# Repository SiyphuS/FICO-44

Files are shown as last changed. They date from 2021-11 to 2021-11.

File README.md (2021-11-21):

# 项目简介
项目名称：FICO-44  
简介视频：https://www.bilibili.com/video/BV1Yh41147wo/

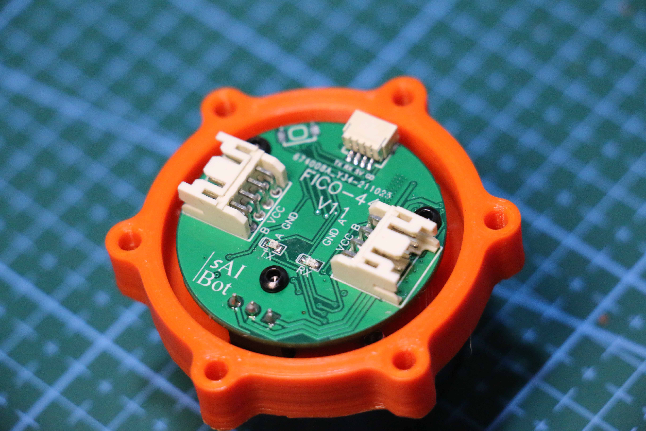
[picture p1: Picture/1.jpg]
主控板


***当前版本仍存在较大缺陷，仅供研究用***  
PCB工程 https://oshwhub.com/zhang_sai/44-guan-jie-qu-dong

## 特点：  
* 基于SIMPLE FOC实现的BLDC FOC（无电流环）控制，控制板集成控制、驱动、编码器于一体； 
* **单个关节80元左右的物料成本**
* 采用集成两级行星减速器，减速比达到30；  
* 除轴承、螺钉、螺母外，所有结构件采用3D打印，大大降低成本。  

## 参数
* 额定电压：16V  
* 额定功率：25W  
* 最大扭矩：1N·M（预估，可能误差较大）  
* 最高转速：80RPM  
* 峰值电流：2.5A  

## 缺陷
* **缺少电流环，高负载、快速运动时极易跑飞，导致当前版本可用性较差。正在考虑保持成本不会大幅上升的解决方案**  
* **3D打印行星减速器的齿轮、齿圈时，打印机精度不足导致装配有问题或者运动过程中阻力过大。使用ENDER-3S打印机，PLA耗材，调教打印机到良好状态时成品率较高，摩擦力可接受。**  

## 提示
* 3D打印的模型需要根据自己的打印机型号和状态进行动态调整后输出STL文件打印，涉及过盈配合和齿轮传动
* 电机一定要让商家做成不带限位的，否则...

## 使用说明
LGT8F328P环境搭建指南：https://oshwhub.com/costar/larduino

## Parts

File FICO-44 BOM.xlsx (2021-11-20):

序号 | 名称 | 数量 | 单价 | 参考链接 | 备注
1 | 轴承 4*7*2.5 | 6 | 1.2 | https://detail.tmall.com/item.htm?id=611796709407&_u=kpuvnbmcd85&skuId=4777422306653
2 | 轴承 优质级B6706ZZ 30*37*4mm | 1 | 5.7 | https://detail.tmall.com/item.htm?id=634910663174&spm=a1z09.2.0.0.9b972e8dt52oDc&_u=kpuvnbma774
3 | PHD2.0线 | 1 | 2 | https://item.taobao.com/item.htm?spm=a1z09.2.0.0.9b972e8dt52oDc&id=621085087437&_u=kpuvnbm18de | 双头同向 长度自选
4 | USB转485模块 | 1 | 2.65 | https://item.taobao.com/item.htm?spm=a1z09.2.0.0.9b972e8dt52oDc&id=537106634975&_u=kpuvnbmf10a
5 | 预埋螺母 3*4*5 | 6 | 0.05 | https://detail.tmall.com/item.htm?id=19528296472&spm=a1z09.2.0.0.9b972e8dt52oDc&_u=kpuvnbm7ba9
6 | 预埋螺母 2*3.5*4 | 12 | 0.05 | 同上
7 | 螺钉 M2*16沉头内六角 | 6 | 0.1 | https://detail.tmall.com/item.htm?id=521341457404&spm=a1z09.2.0.0.9b972e8dt52oDc&_u=kpuvnbm6b46
8 | 螺钉 M2*4圆头内六角 | 3 | 0.1 | https://detail.tmall.com/item.htm?id=521341125910&_u=kpuvnbma651&skuId=4321899528386
9 | 螺钉 M2*6圆头内六角 | 3 | 0.1 | 同上
10 | 螺钉 M2*5内六角 | 6 | 0.1 | https://detail.tmall.com/item.htm?id=521303174891&spm=a1z09.2.0.0.9b972e8dt52oDc&_u=kpuvnbm53db
11 | 螺钉 M3*6圆头十字 | 6 | 0.1 | https://detail.tmall.com/item.htm?id=521140346640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
12 | 2804云台电机 | 1 | 35 | https://detail.1688.com/offer/602427933286.html?spm=a360q.8274423.0.0.49c84c9awkLhvP | 给厂家备注不需要限位
13 | 润滑脂 | 1 | 8 | https://item.taobao.com/item.htm?spm=a1z09.2.0.0.779d2e8dTmLkBQ&id=622524727704&_u=kpuvnbm0513

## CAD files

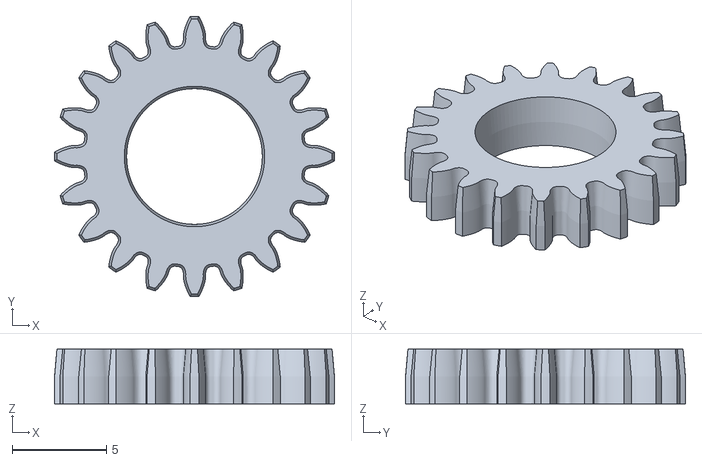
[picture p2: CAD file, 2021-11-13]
3D file/STL/44xxc-2.stl
14.9 x 14.9 x 2.89

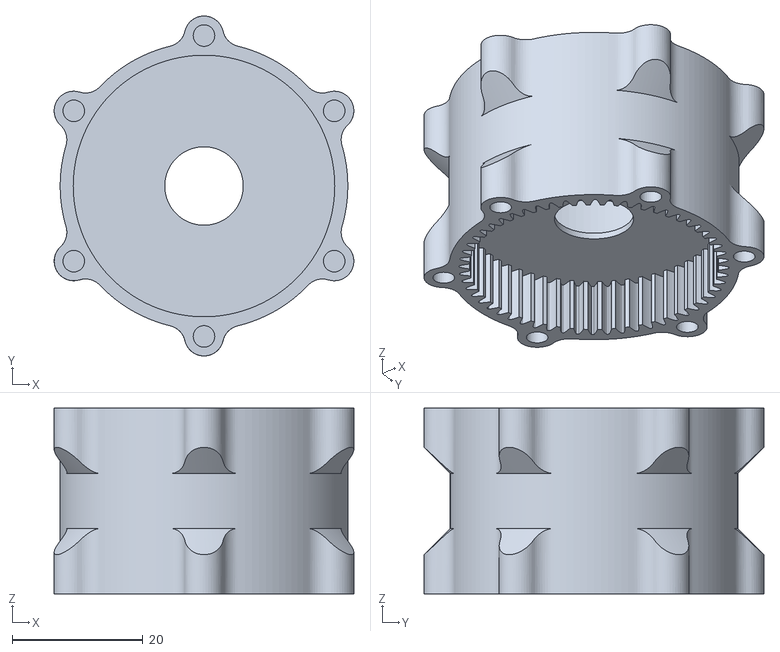
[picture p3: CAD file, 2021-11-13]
3D file/STL/44wcq.stl
45.8 x 52.0 x 28.4

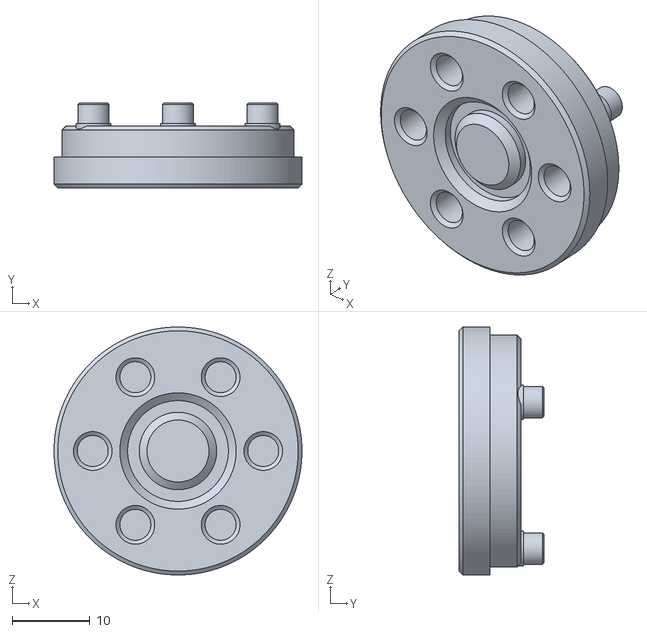
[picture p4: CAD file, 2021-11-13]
3D file/STL/44scz.stl
32.0 x 11.0 x 32.0

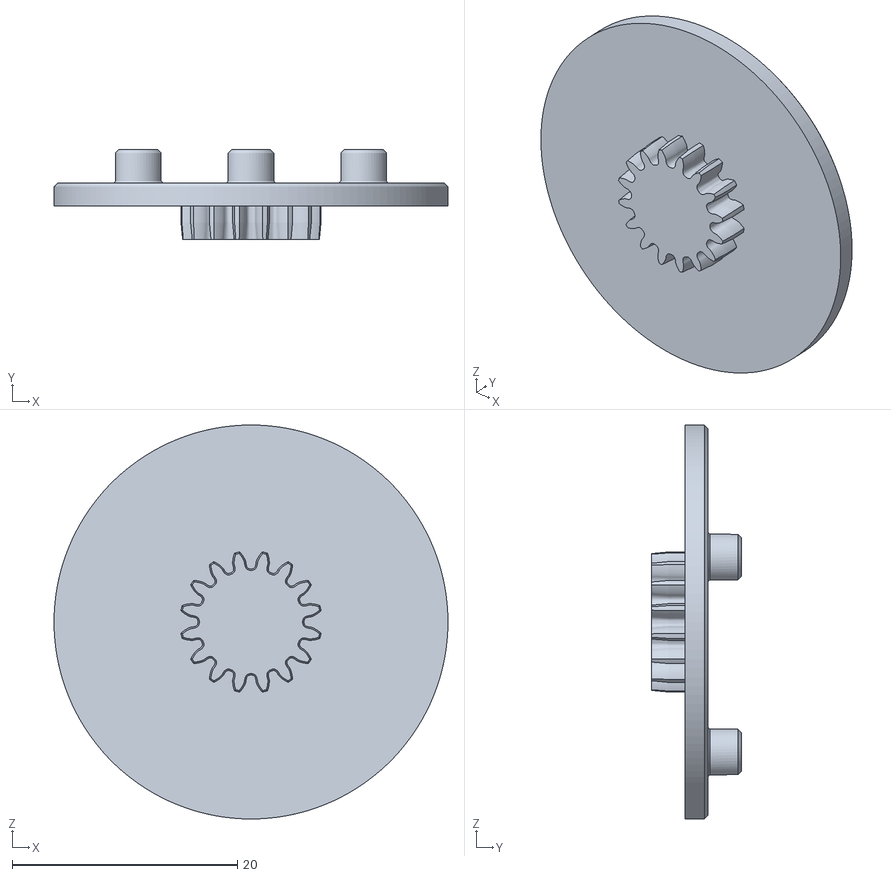
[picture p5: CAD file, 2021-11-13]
3D file/STL/44xxj.stl
35.0 x 8.00 x 35.0

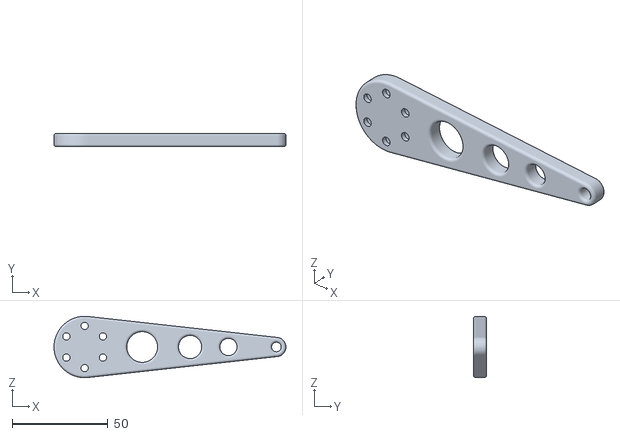
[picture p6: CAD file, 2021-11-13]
3D file/STL/44lb.stl
121.0 x 7.00 x 32.0

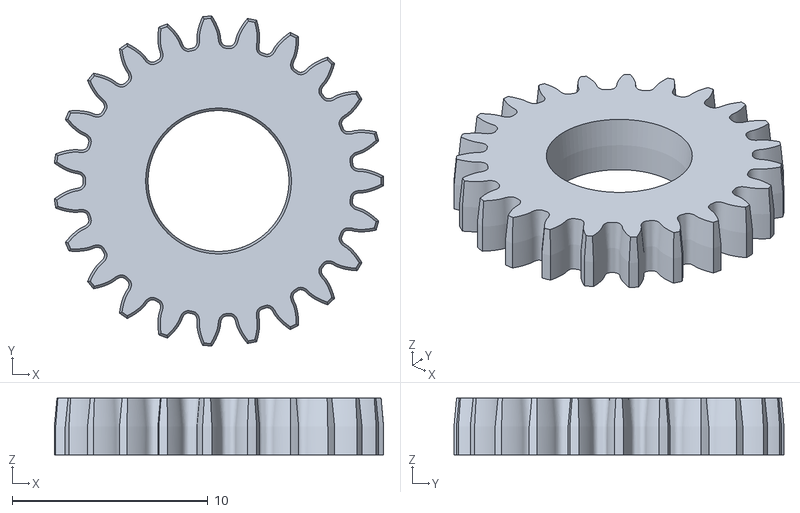
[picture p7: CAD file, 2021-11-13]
3D file/STL/44xxc-1.stl
16.8 x 16.9 x 2.89

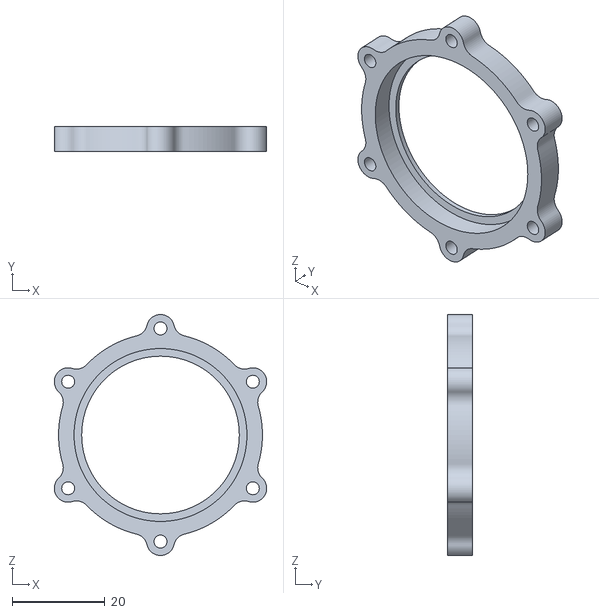
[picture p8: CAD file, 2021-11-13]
3D file/STL/44zg.stl
45.8 x 5.30 x 52.0

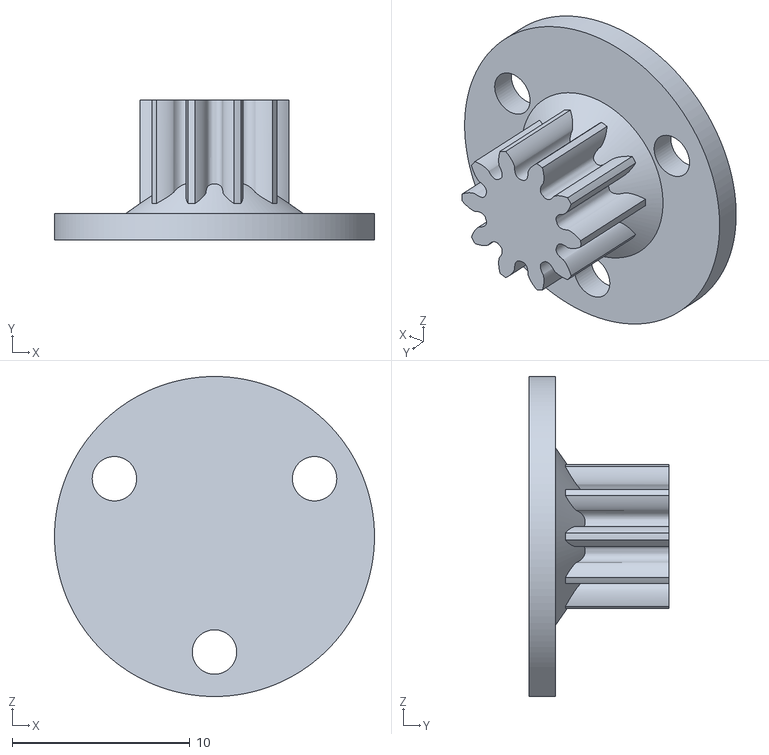
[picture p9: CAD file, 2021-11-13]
3D file/STL/44srz.stl
18.0 x 7.90 x 18.0

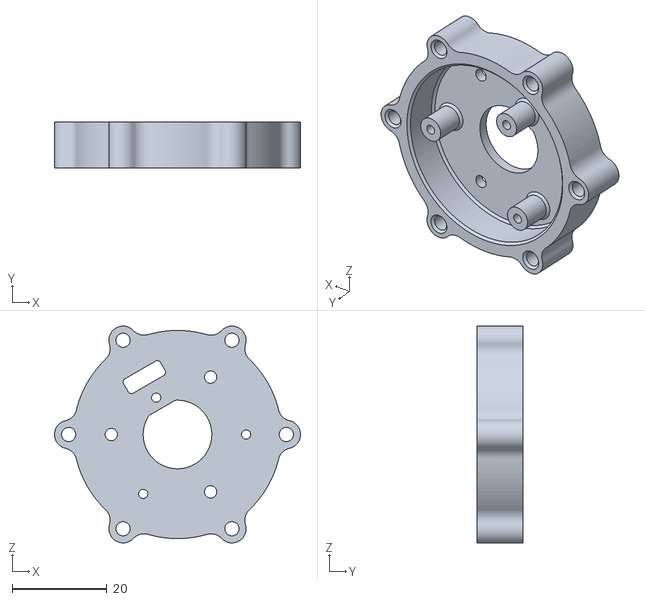
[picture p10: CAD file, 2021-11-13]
3D file/STL/44djz.stl
52.0 x 9.70 x 45.8

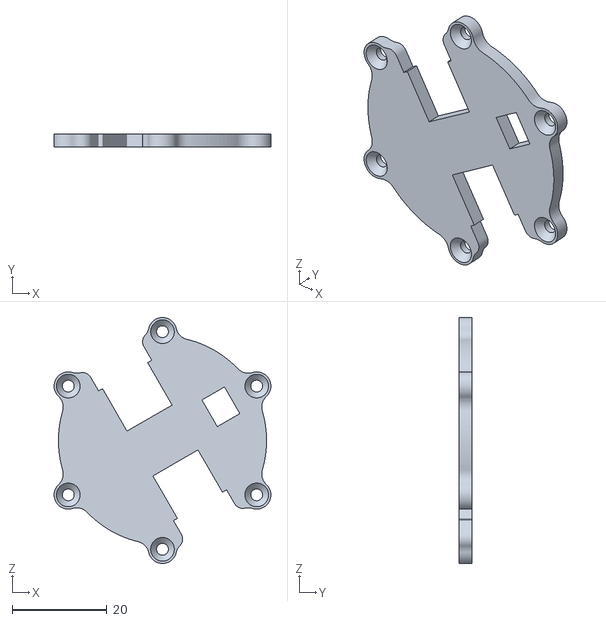
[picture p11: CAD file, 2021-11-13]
3D file/STL/44dg.stl
45.8 x 2.80 x 52.0

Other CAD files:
3D file/30-37-4轴承.prt
3D file/4-7-2_5轴承.prt
3D file/44二级太阳轮1.prt
3D file/44外齿圈.prt
3D file/8-12-3磁环.prt
3D file/PCB/___0_1_1_15__1.prt
3D file/PCB/___0_1_1_15__2.prt
3D file/PCB/___0_1_1_15__3.prt
3D file/PCB/___0_1_1_15__4.prt
3D file/PCB/___0_1_1_15__5.prt
3D file/PCB/___0_1_1_15__6.prt
3D file/PCB/___0_1_1_15__7.prt
3D file/PCB/___0_1_1_15__8.prt
3D file/PCB/___0_1_1_15__9.prt
3D file/PCB/compound-157.prt
3D file/PCB/compound-51006_1.prt
3D file/PCB/compound-51006_2.prt
3D file/PCB/compound-51006_3.prt
3D file/PCB/compound-51006_4.prt
3D file/PCB/compound-51006_5.prt
3D file/PCB/compound-51006_6.prt
3D file/PCB/compound-51006_7.prt
3D file/PCB/compound-51006_8.prt
3D file/PCB/compound-51006_9.prt
3D file/PCB/compound-6247_1.prt
3D file/PCB/compound-6247_10.prt
3D file/PCB/compound-6247_11.prt
3D file/PCB/compound-6247_12.prt
3D file/PCB/compound-6247_2.prt
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

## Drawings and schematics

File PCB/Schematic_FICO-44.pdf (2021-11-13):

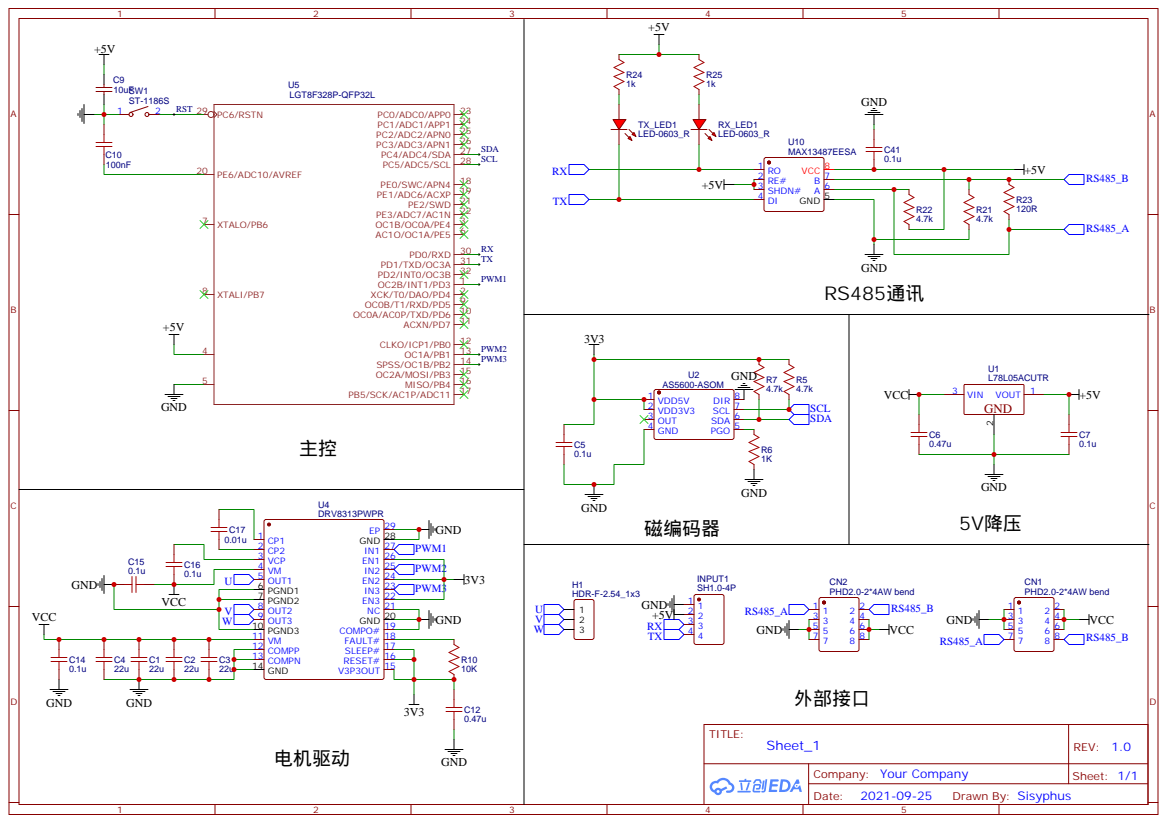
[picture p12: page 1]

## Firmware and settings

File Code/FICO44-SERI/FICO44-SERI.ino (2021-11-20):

/**
   Comprehensive BLDC motor control example using magnetic sensor

   Using serial terminal user can send motor commands and configure the motor and FOC in real-time:
   - configure PID controller constants
   - change motion control loops
   - monitor motor variabels
   - set target values
   - check all the configuration values

   See more info in docs.simplefoc.com/commander_interface
*/
#include <SimpleFOC.h>

// magnetic sensor instance - SPI
//MagneticSensorSPI sensor = MagneticSensorSPI(AS5147_SPI, 10);
// magnetic sensor instance - MagneticSensorI2C
MagneticSensorI2C sensor = MagneticSensorI2C(AS5600_I2C);
// magnetic sensor instance - analog output
// MagneticSensorAnalog sensor = MagneticSensorAnalog(A1, 14, 1020);


// BLDC motor & driver instance
BLDCMotor motor = BLDCMotor(7);
BLDCDriver3PWM driver = BLDCDriver3PWM(3, 9, 10);
// Stepper motor & driver instance
//StepperMotor motor = StepperMotor(50);
//StepperDriver4PWM driver = StepperDriver4PWM(9, 5, 10, 6,  8);

// commander interface
Commander command = Commander(Serial);
void onMotor(char* cmd) {
  command.motor(&motor, cmd);
}

void setup() {
  Wire.setClock(1000000);
  // initialise magnetic sensor hardware
  sensor.init();
  // link the motor to the sensor
  motor.linkSensor(&sensor);

  // driver config
  // power supply voltage [V]
  driver.voltage_power_supply = 16;
  driver.init();
  // link driver
  motor.linkDriver(&driver);

  // choose FOC modulation
  motor.foc_modulation = FOCModulationType::SpaceVectorPWM;

  // set control loop type to be used
  motor.controller = MotionControlType::angle;

  // contoller configuration based on the control type
  motor.PID_velocity.P = 0.05;
  motor.PID_velocity.I = 3;
  motor.PID_velocity.D = 0;
  motor.PID_velocity.output_ramp = 1000;
  // default voltage_power_supply
  motor.voltage_limit = 9;

  // velocity low pass filtering time constant
  motor.LPF_velocity.Tf = 0.01;

  // angle loop controller
  motor.P_angle.P = 20;
  motor.P_angle.output_ramp = 1000;
  
  // angle loop velocity limit
  motor.velocity_limit = 40;

  // use monitoring with serial for motor init
  // monitoring port
  Serial.begin(115200);
  // comment out if not needed
  motor.useMonitoring(Serial);

  // initialise motor
  motor.init();
  // align encoder and start FOC
  motor.initFOC();

  // set the inital target value
  motor.target = 0;

  // define the motor id
  command.add('A', onMotor, "motor");

  // Run user commands to configure and the motor (find the full command list in docs.simplefoc.com)
  Serial.println(F("Motor commands sketch | Initial motion control > torque/voltage : target 2V."));

  _delay(1000);
}


void loop() {
  // iterative setting FOC phase voltage
  motor.loopFOC();

  // iterative function setting the outter loop target
  // velocity, position or voltage
  // if tatget not set in parameter uses motor.target variable
  motor.move();
  
  //motor.monitor();
  // user communication
  command.run();
}
